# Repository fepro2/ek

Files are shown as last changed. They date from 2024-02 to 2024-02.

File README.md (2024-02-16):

# ek
Experimental Kit (EK) for an Agile Design Process of an Industrial Multihead Weigher

This project contains the following files to build up your own EK:

    sensing: 3D printed components stl files and standard parts - as well as a assembly stl

    signal conditioning: hardware components and drawings to build the signal amplification circuit board
    
    signal processing: arduino and python code

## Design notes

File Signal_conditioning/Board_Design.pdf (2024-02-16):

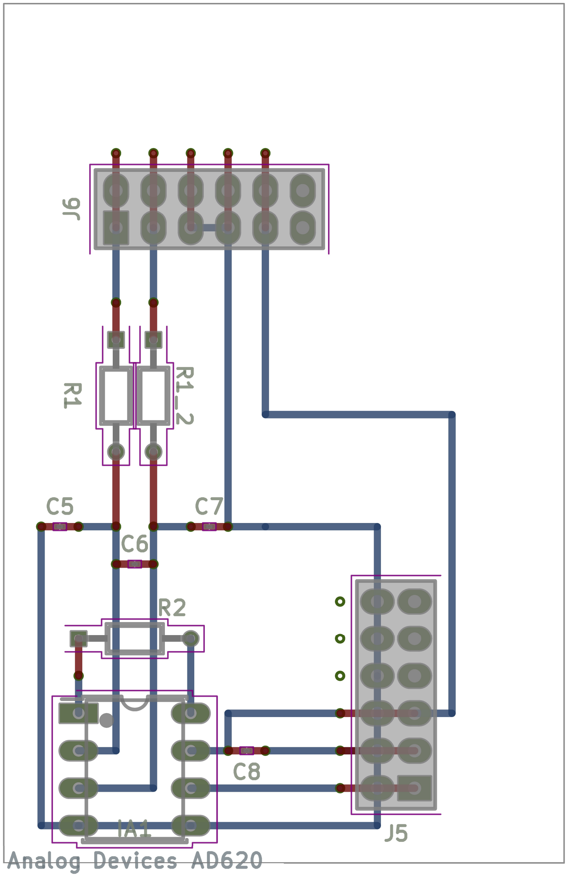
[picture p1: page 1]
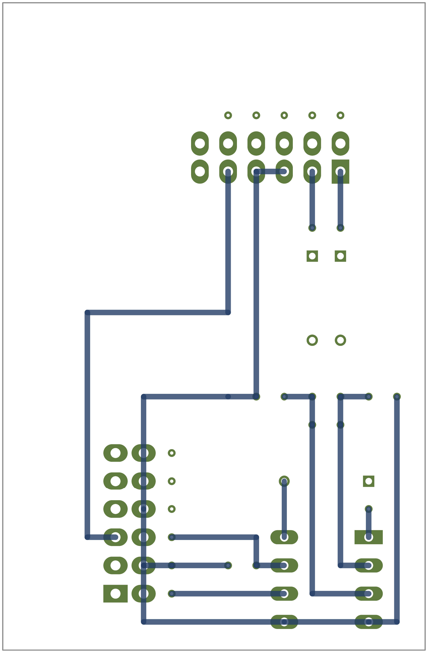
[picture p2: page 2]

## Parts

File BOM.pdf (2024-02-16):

## BOM Experimental Kit

03.02.2024
Author: Felix Profe

### Sensing Parts

3D Print Components | Qty
Load Cell Sauter CP 3-2Y1 | 1
2076240_WB_body | 1
2076259_bracket | 1
2076260_diagonal_brace_rear | 2
2076262_diagonal_brace_front | 2
2076268_limit_stop_bolt | 1
2076269_sleeve_bearing_lever | 1
2076272_lever | 1
2076275_connection | 1
2076277_flap | 1
2076278_sleeve_bearing_flaps | 2
2076282_excentric_bolt | 1
Standard parts WB | Qty
Screw ISO4017-M4-30 | 2
Screw ISO4017-M4-20 | 2
Screw ISO4017-M4-25 | 2
Nut ISO10511-M4 | 5
Washer ISO7093-4.3 | 5
Washer ISO7089-4.3 | 1
Standard parts Bracket | Qty
Screw ISO4017-M6-45 | 2
Screw ISO4017-M6-55 | 6
Screw ISO4017-M6-90 | 2
Nut ISO10511-M6 | 4
Wing nut DIN315-M6 | 6

### Signal Conditioning Parts

Component | Qty
External power supply 0-12V | 1
Instrumentation amplifier AD620ANZ | 1
IC-Dip Socket TE CONNECTIVITY 1-2199298-2 | 1
Arduino jumper wire male-male | 4
Breadboard Epoxy 100 x 160 mm 2.54 mm | 1
Wago 233 2.54mm Pitch, 6 Contact | 2
Resistor R1 = 500 Ohm | 2
Resistor R_G = 220 Ohm | 1
Capacitor C_C = 100nF | 2
Capacitor C_D = 1µF | 1
Capacitor 100nF | 1

### Signal Processing Parts

Component | Qty
Arduino Due | 1

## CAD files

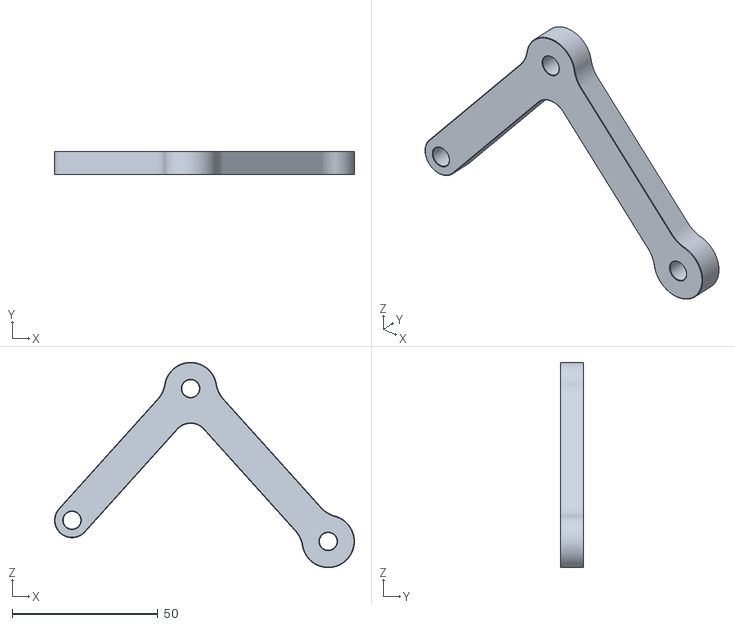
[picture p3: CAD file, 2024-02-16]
Sensing/3D-Print-Parts/2076262_diagonal_brace_front.stl
102.7 x 8.00 x 70.3

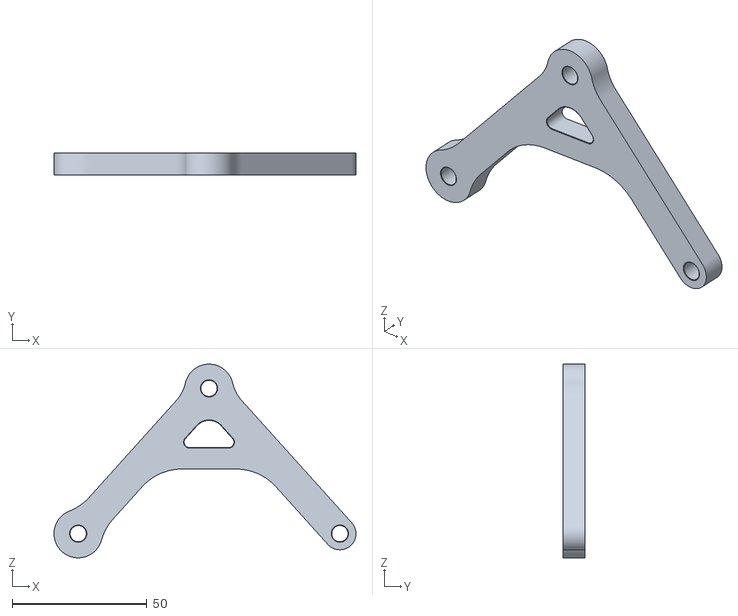
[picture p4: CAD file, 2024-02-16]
Sensing/3D-Print-Parts/2076260_diagonal_brace_rear.stl
112.2 x 8.00 x 72.0

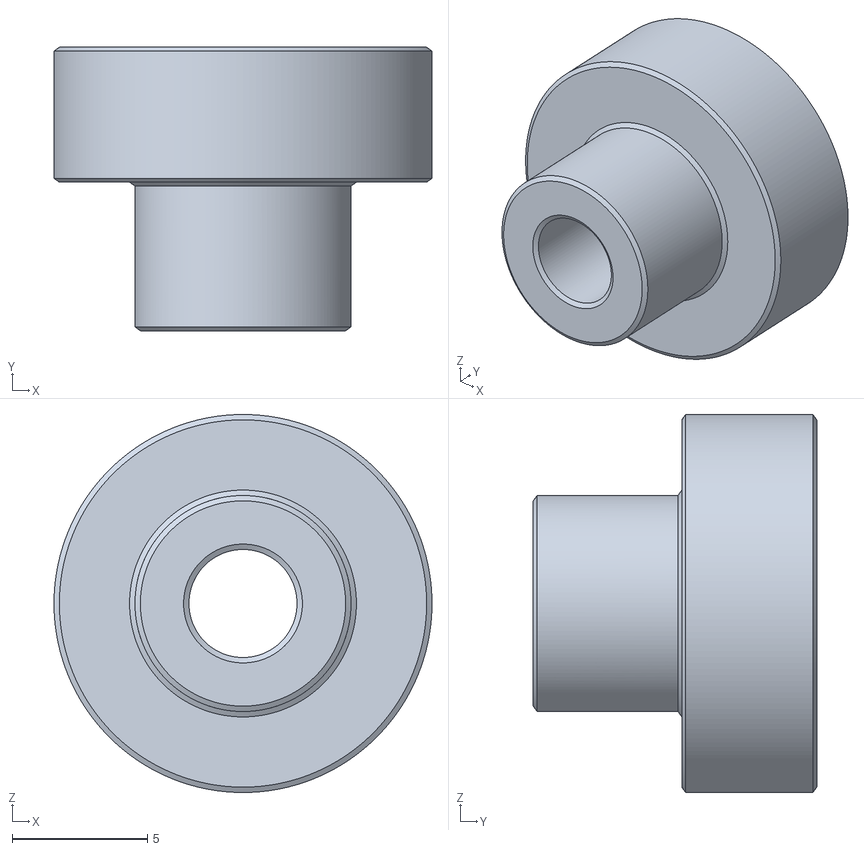
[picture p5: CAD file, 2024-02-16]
Sensing/3D-Print-Parts/2076269_sleeve_bearing_lever.stl
14.0 x 10.5 x 14.0

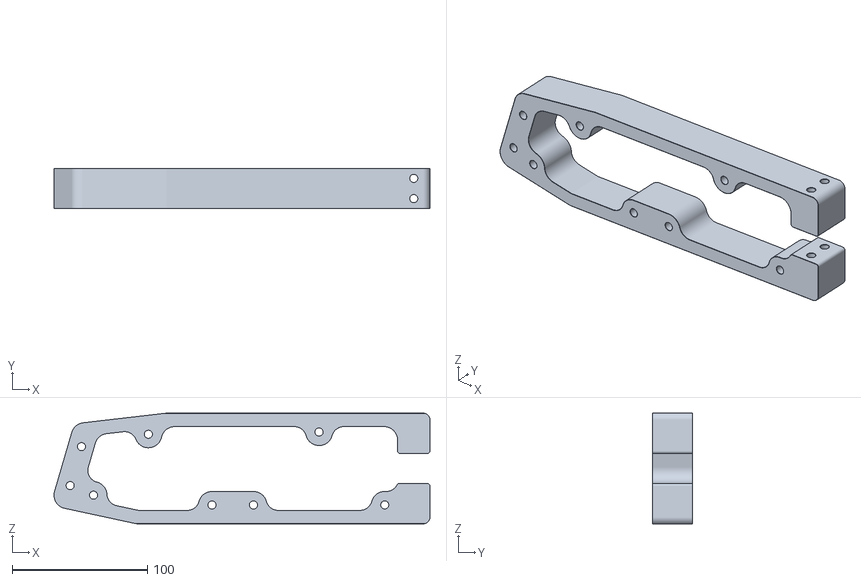
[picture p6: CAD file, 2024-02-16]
Sensing/3D-Print-Parts/2076259_bracket.stl
278.4 x 29.8 x 82.0

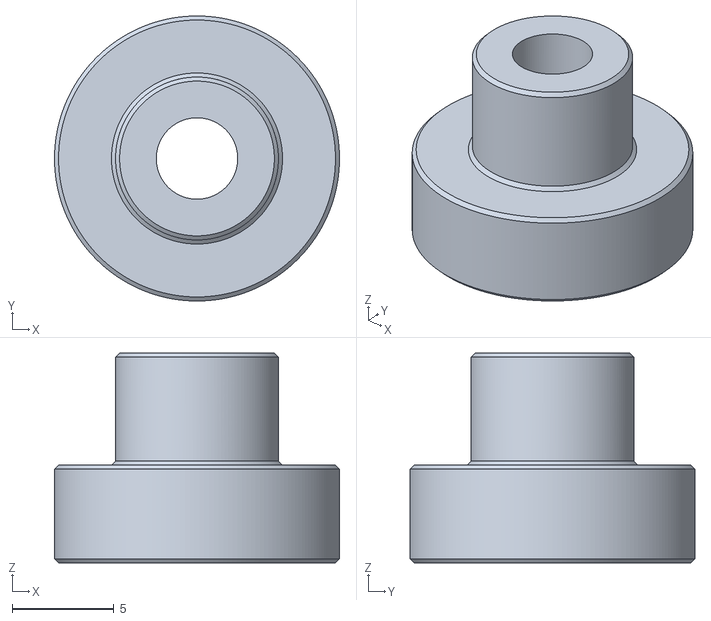
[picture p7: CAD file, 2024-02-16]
Sensing/3D-Print-Parts/2076278_sleeve_bearing_flaps.stl
14.0 x 14.0 x 10.3

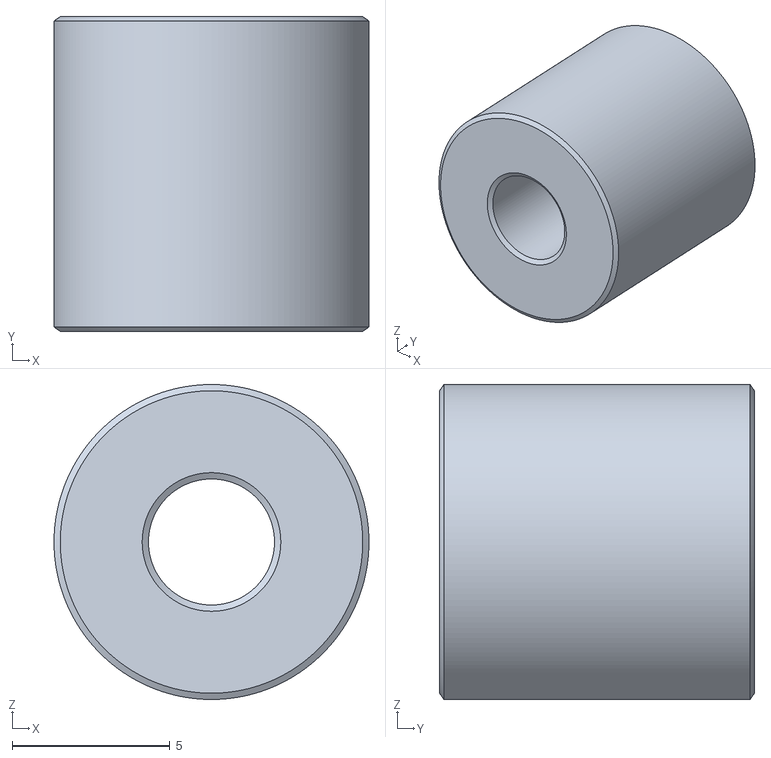
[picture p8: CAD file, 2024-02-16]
Sensing/3D-Print-Parts/2076268_limit_stop_bolt.stl
10.00 x 10.0 x 10.0

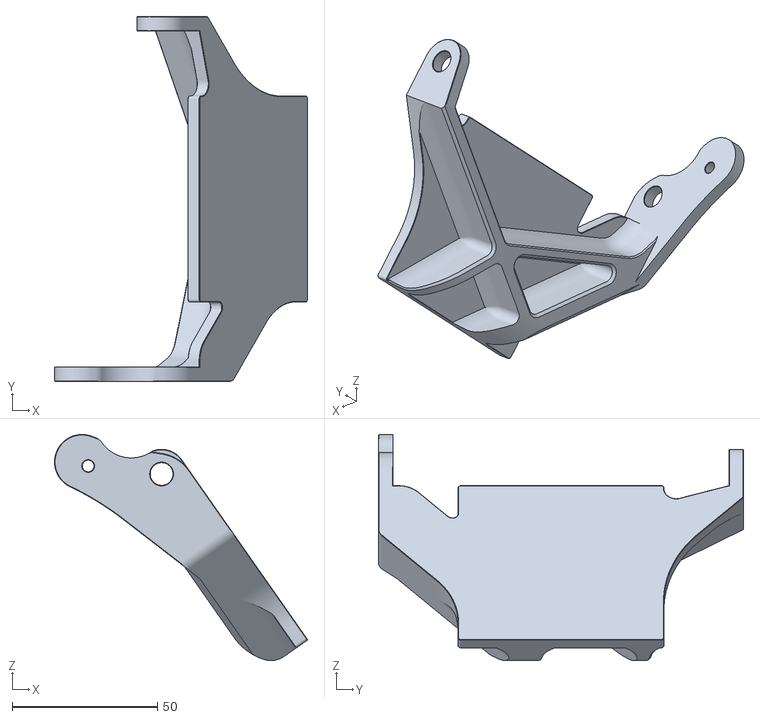
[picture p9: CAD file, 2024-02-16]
Sensing/3D-Print-Parts/2076277_flap.stl
87.2 x 125.8 x 77.9

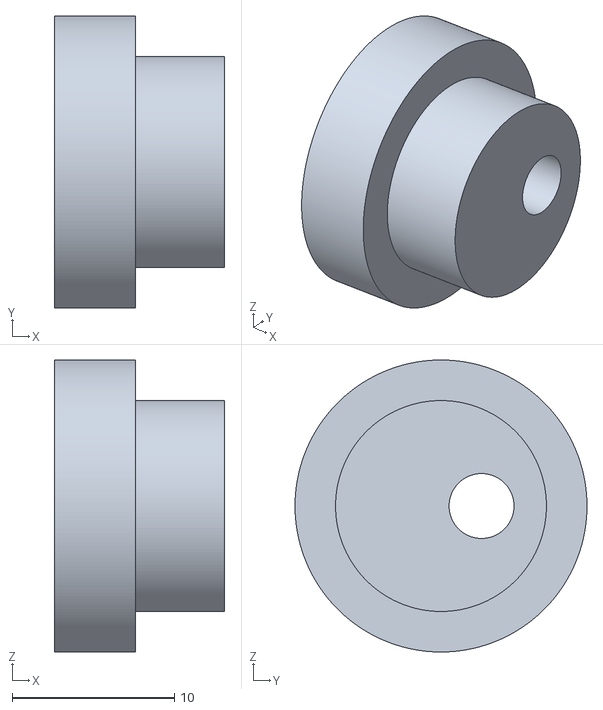
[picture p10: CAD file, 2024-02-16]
Sensing/3D-Print-Parts/2076282_excentric_bolt.stl
10.5 x 18.0 x 18.0

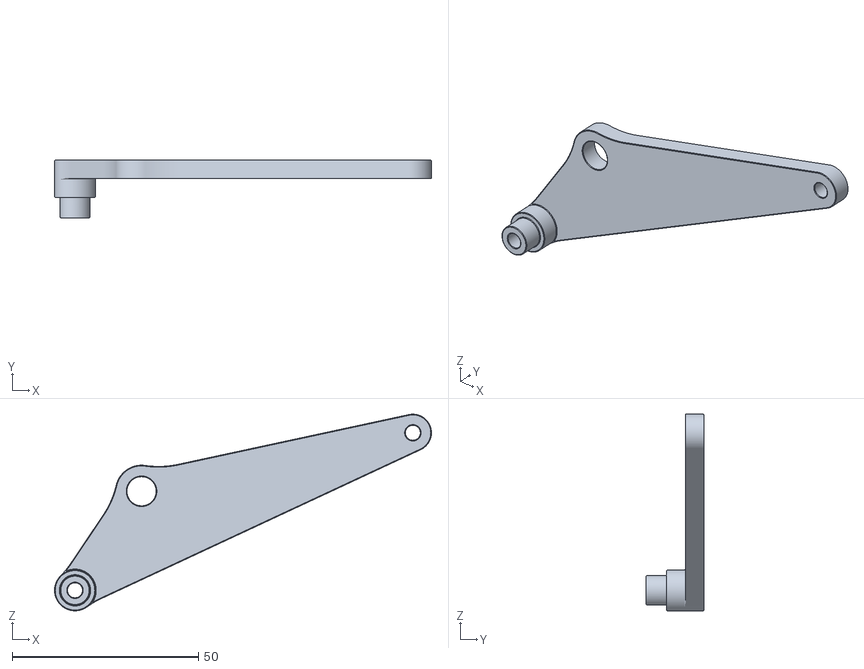
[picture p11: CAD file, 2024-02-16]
Sensing/3D-Print-Parts/2076272_lever.stl
101.1 x 15.5 x 52.8

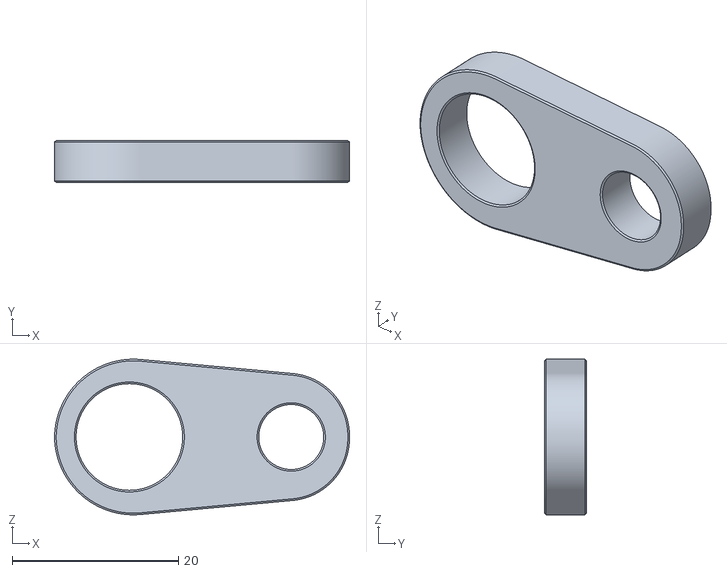
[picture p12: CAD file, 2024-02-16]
Sensing/3D-Print-Parts/2076275_connection.stl
35.4 x 5.00 x 18.7

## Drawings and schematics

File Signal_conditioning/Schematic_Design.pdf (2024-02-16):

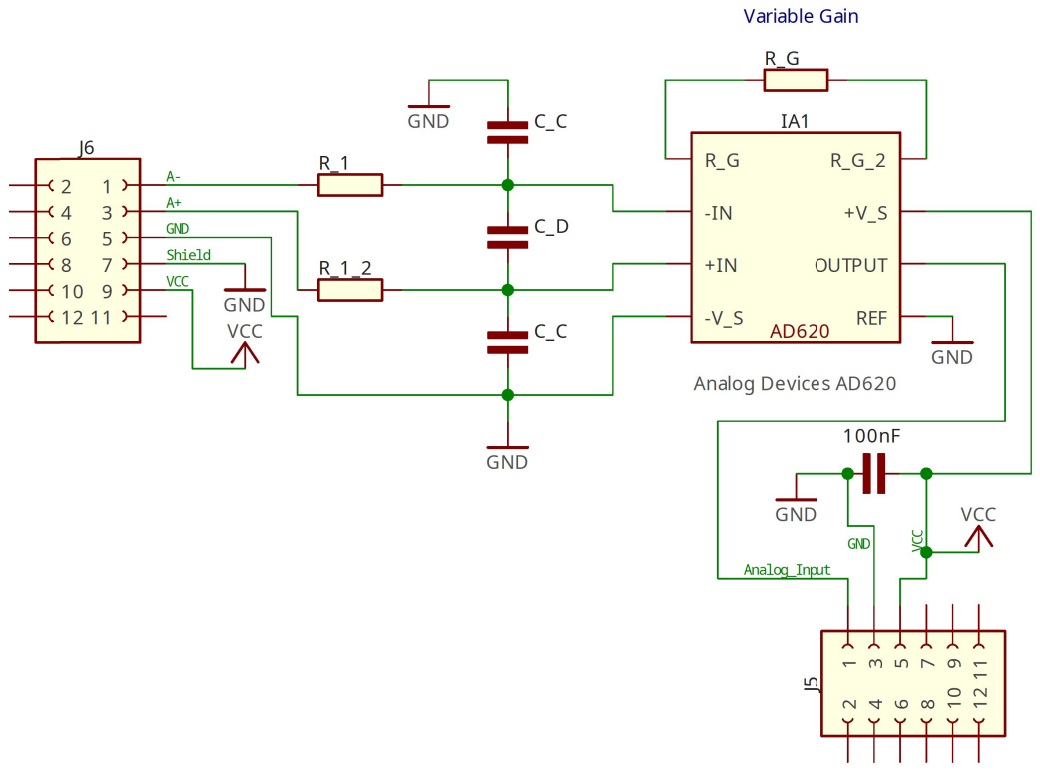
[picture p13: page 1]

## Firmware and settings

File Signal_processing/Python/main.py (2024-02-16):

#!/usr/bin/env python
# -*- coding: utf-8 -*-

# Recording and analysing of experimental kit weigh signal
# Felix Profe
# 2024-02-03

import datetime

from functions import *

if __name__ == "__main__":
    FILENAME_CONFIG = "ek_config.json"
    ek_config = load_json(FILENAME_CONFIG)
    
    # Parameter
    PORT = ek_config["port"]
    BAUD_RATE = ek_config["baud_rate"]
    TARE_VALUE = ek_config["tare_value"]
    CALIBRATION_LOAD_G = ek_config["calibration_load_g"]
    CALIBRATION_LOAD = ek_config["calibration_load"]
    CALIBRATION_FACTOR = (CALIBRATION_LOAD - TARE_VALUE) / CALIBRATION_LOAD_G
    STATIC_AVERAGING_STEPS = ek_config["static_averaging_steps"]
    FILTER_ORDER_1 = ek_config["filter_order_1"]
    FILTER_CUTOFF_FREQUENCY_1 = ek_config["filter_cutoff_frequency_1"]  # Hz
    FILTER_ORDER_2 = ek_config["filter_order_2"]
    FILTER_CUTOFF_FREQUENCY_2 = ek_config["filter_cutoff_frequency_2"]  # Hz
    RECORD_DURATION = ek_config["record_duration"]  # s
    CALIBRATION = ek_config["calibration"]
    TARING = ek_config["taring"]
    TARING_DURATION = ek_config["taring_duration"]
    CALIBRATION_DURATION = ek_config["calibration_duration"]
    LOWEST_FREQUENCY_HZ = ek_config["lowest_frequency_hz"]

    dateTime = datetime.datetime.now()
    dateTimeString = dateTime.strftime("%Y%m%d_%H%M")
    shorttext = ek_config["event_name"]
    shorttext = str(dateTimeString) + "_" + shorttext
    path = "results"
        
    if TARING:
        TARE_VALUE = tare(PORT, BAUD_RATE, record_duration=TARING_DURATION)
        ek_config["tare_value"] = TARE_VALUE
        ek_config["taring"] = False
        write_json(ek_config, FILENAME_CONFIG)
        
    if CALIBRATION:
        CALIBRATION_LOAD, CALIBRATION_LOAD_G = calibrate(
                PORT,
                BAUD_RATE,
                CALIBRATION_LOAD_G,
                record_duration=CALIBRATION_DURATION
        )
        ek_config["calibration_load"] = CALIBRATION_LOAD
        ek_config["calibration_load_g"] = CALIBRATION_LOAD_G
        CALIBRATION_FACTOR = (CALIBRATION_LOAD - TARE_VALUE) / CALIBRATION_LOAD_G
        ek_config["calibration"] = False
        write_json(ek_config, FILENAME_CONFIG)

    if ek_config["recording"]:
        data = read_serial_port(PORT, BAUD_RATE, RECORD_DURATION)
        timevec, adc_g, sampling_rate, sampling_frequency = process_measurement(data, TARE_VALUE, CALIBRATION_FACTOR)
        if ek_config["save_raw_measurement"]:
            dict = {}
            dict["time"] = timevec.tolist()
            dict["adc_g"] = adc_g
            path_raw_measurement = "raw/" + shorttext + ".json"
            write_json(dict, path_raw_measurement)     
    else:
        timevec, adc_g, sampling_rate, sampling_frequency = read_raw_measurement(ek_config["path_raw_measurement"])
        print("Mean ADC_g: ", np.mean(adc_g), " g")
        
    print("Mean ADC_g_static: ", np.mean(adc_g[STATIC_AVERAGING_STEPS:]), " g")

    adc_g_filtered_1 = butter_lowpass_filter(
            adc_g,
            FILTER_CUTOFF_FREQUENCY_1,
            sampling_frequency,
            FILTER_ORDER_1
    )
    adc_g_filtered_2 = butter_lowpass_filter(
            adc_g_filtered_1,
            FILTER_CUTOFF_FREQUENCY_2,
            sampling_frequency,
            FILTER_ORDER_2
    )
    plt.plot(timevec, adc_g)
    plt.plot(timevec, adc_g_filtered_1)
    plt.plot(timevec, adc_g_filtered_2)
    plt.show()

    plt.plot(adc_g)
    plt.show()

    # Frequency Analysis
    lower_border = input("Lower Border:")
    lower_border = int(lower_border)

    upper_border = input("Upper Border:")
    upper_border = int(upper_border)

    frequency_vector, amplitude_vector = analyze_frequencies(
            adc_g,
            sampling_rate,
            lower_border,
            upper_border,
            ek_config,
            path,
            shorttext
    )

    if ek_config["save_results"]:
        text = shorttext + "_timesignal"
        dict = {}
        dict["time_ms"] = timevec
        dict["signal_adc"] = adc_g
        dict["signal_adc_filter_o" + str(FILTER_ORDER_1) + "f" + str(FILTER_CUTOFF_FREQUENCY_1)] = adc_g_filtered_1
        dict["signal_adc_filter_o" + str(FILTER_ORDER_2) + "f" + str(FILTER_CUTOFF_FREQUENCY_2)] = adc_g_filtered_2
        save_excel(dict, path, text)

        textfft = shorttext + "_fft"
        dict = {}
        dict["frequency_hz"] = frequency_vector
        dict["amplitude"] = amplitude_vector
        save_excel(dict, path, textfft)

        frequency_peaks, amplitude_peaks = detectPeaks(frequency_vector, amplitude_vector, plots=True)
        textPeak = shorttext + "_fftPeaks"
        dict = {}
        dict["frequency_hz"] = frequency_peaks
        dict["amplitude"] = amplitude_peaks
        save_excel(dict, path, textPeak)

        peakFrequency = findFrequencyOfHighestAmplitude(frequency_peaks, amplitude_peaks, LOWEST_FREQUENCY_HZ)
        print(peakFrequency, "Hz")

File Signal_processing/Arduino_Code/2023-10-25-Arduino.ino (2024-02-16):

#include <SPI.h>
#include <SD.h>

long maxTimeMs = 0;
float x;

void setup() {
  // Open serial communications and wait for port to open:
  Serial.begin(250000);
  while (!Serial) {
    ; // wait for serial port to connect. Needed for native USB port only
  }
  analogReadResolution(12);
}

void loop(){
  while (!Serial.available());
  x = Serial.readString().toInt();
  float maxTime = float(x); // in s
  maxTimeMs = long(maxTime * 1000)+ millis();
  //Serial.println("\\#Zeit_µs;Messwert");
  while(millis() < maxTimeMs)
  {
      Serial.println( String(micros()) + ";" + String(analogRead(0)));
  }
  Serial.println("\\#Done");
}
